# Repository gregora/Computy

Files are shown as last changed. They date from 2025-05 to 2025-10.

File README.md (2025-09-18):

# Computy

An STM32 based flight computer

## Features

- **STM32F205 MCU**
- **BNO055 IMU** and **magnetometer**
- **GNSS** via UART
- **6 PWM** outputs for servos
- Receiver connection via UART
- **433MHz CC1101** telemetry radio

## Hardware

Board specifictions:
- **50mm x 100mm** board size
- Four **M3** mounting holes
- **25Mhz** external oscilator

KiCAD files can be found in `/PCB` directory.

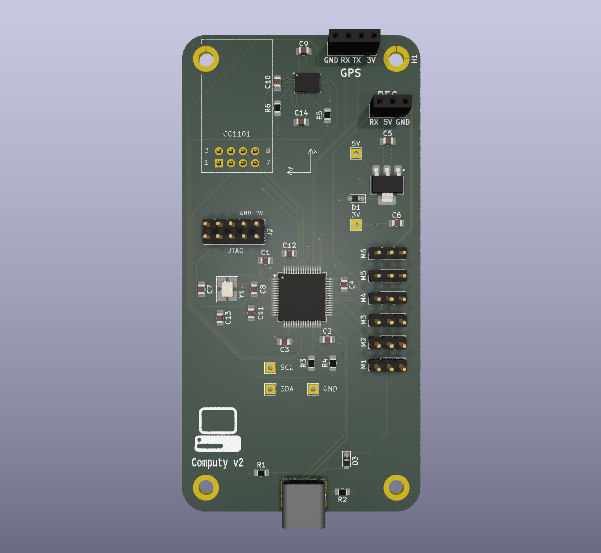
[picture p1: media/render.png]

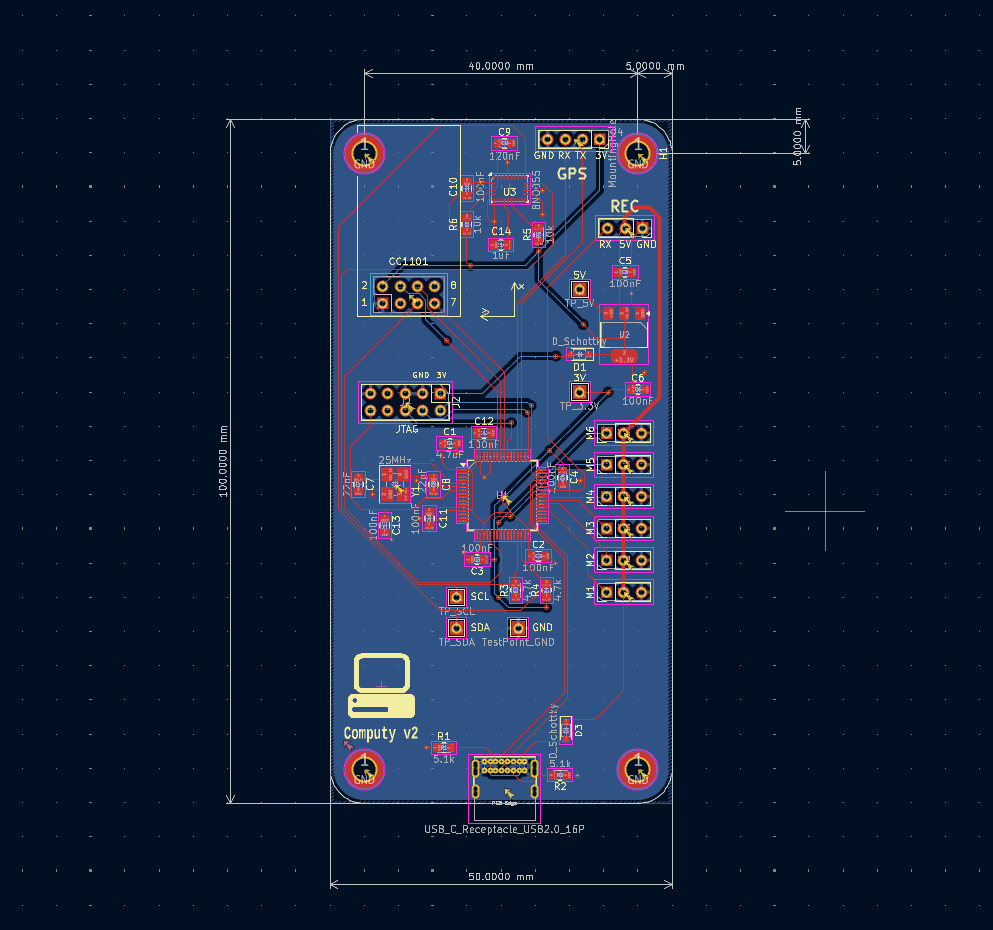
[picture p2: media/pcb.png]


## Firmware

MCU is programmed with CubeIDE. Full project is located in `firmware/Computy`.

### Dependencies

- **[stm32-nmea-gps-hal](https://github.com/sztvka/stm32-nmea-gps-hal)** (**modified** and **included**)

### Setup

Before you can build and upload the project to your Computy board, you have to create a `coordinates.h` header file in `firmware/Computy/Core/Inc` in which you have to define `TARGET_LAT` and `TARGET_LONG` variables.
Because the geolocation is sensitive, this file is included in `.gitignore` and is thus hidden.

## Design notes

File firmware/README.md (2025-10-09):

# Firmware specifications

## Operation modes

| Mode | Name | Description |
|---|---|---|
| 0 | Manual | Direct output to PWM signals |
| 1 | Take-off | Assume 10 degree pitch up attitude |
| 2 | Fly-by-wire | Control angular velocities |
| 3 | Automatic | Fly the mission autonomously |
| 255  | Recovery | Mode 0, only exit when all switches are up |

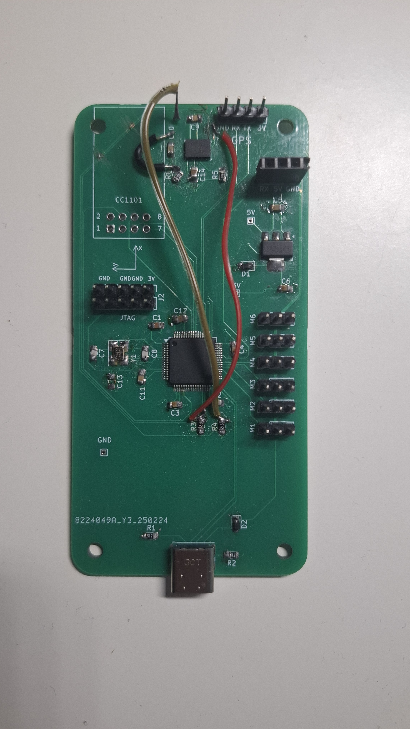
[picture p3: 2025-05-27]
media/Computy.jpg

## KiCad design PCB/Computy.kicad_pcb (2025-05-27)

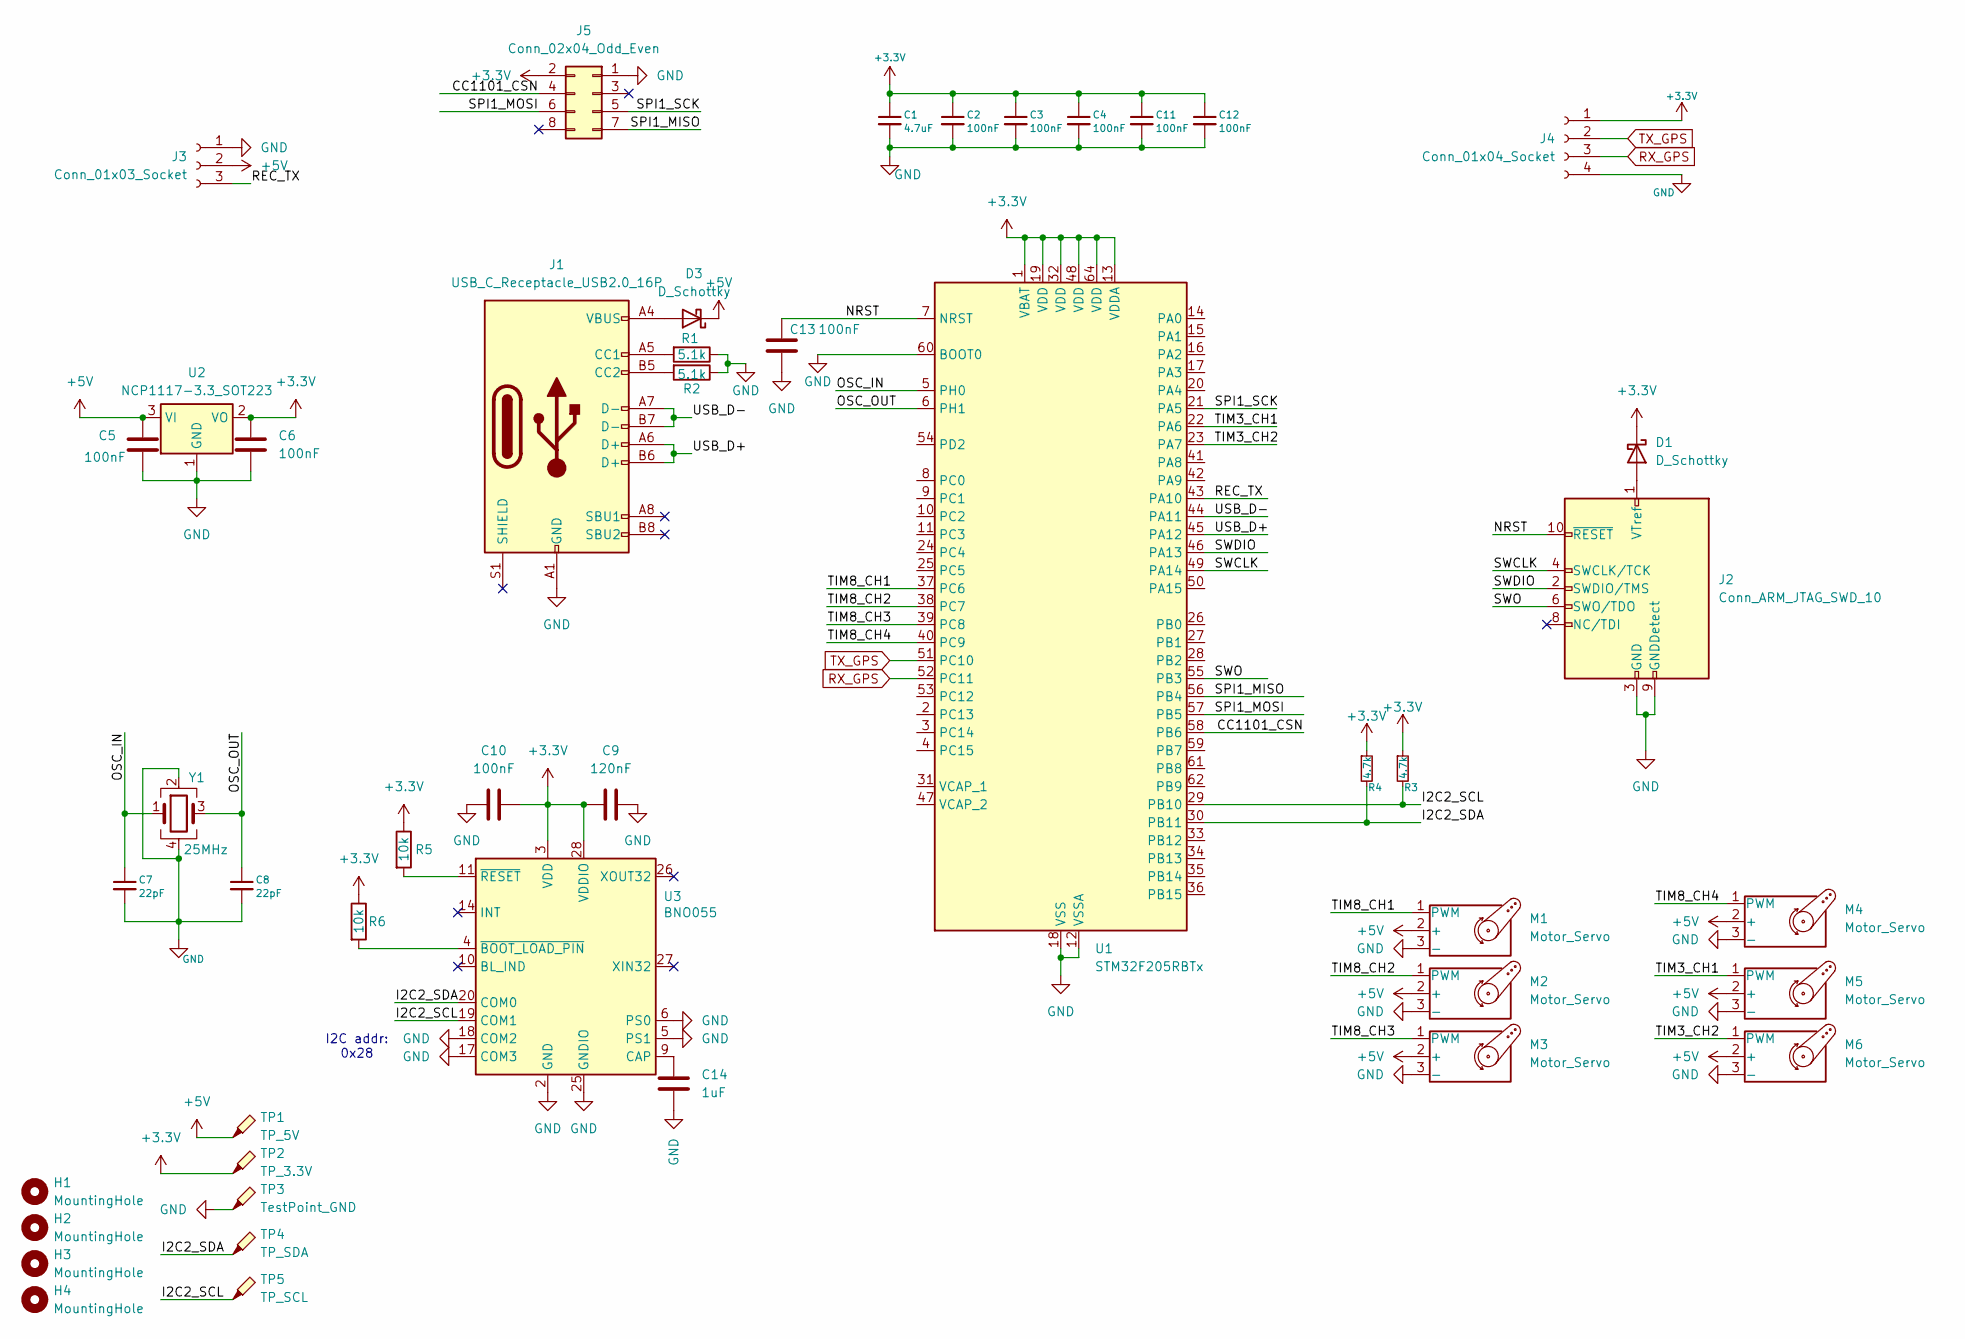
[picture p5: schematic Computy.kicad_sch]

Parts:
C1: 4.7uF; C_0805_2012Metric_Pad1.18x1.45mm_HandSolder
C2, C3, C4, C5, C6, C10, C11, C12, C13: 100nF; C_0805_2012Metric_Pad1.18x1.45mm_HandSolder
C7, C8: 22pF; C_0805_2012Metric_Pad1.18x1.45mm_HandSolder
C9: 120nF; C_0805_2012Metric_Pad1.18x1.45mm_HandSolder
C14: 1uF; C_0805_2012Metric_Pad1.18x1.45mm_HandSolder
D1, D3: D_Schottky; D_SOD-323_HandSoldering
H1, H2, H3, H4: MountingHole; MountingHole_3.2mm_M3_DIN965_Pad
J1: USB_C_Receptacle_USB2.0_16P; USB_C_Receptacle_GCT_USB4085
J2: Conn_ARM_JTAG_SWD_10; PinHeader_2x05_P2.54mm_Vertical
J3: Conn_01x03_Socket; PinSocket_1x03_P2.54mm_Vertical
J4: Conn_01x04_Socket; PinSocket_1x04_P2.54mm_Vertical
J5: Conn_02x04_Odd_Even; PinSocket_2x04_P2.54mm_Vertical
M1, M2, M3, M4, M5, M6: Motor_Servo; PinHeader_1x03_P2.54mm_Vertical
R1, R2: 5.1k; R_0805_2012Metric_Pad1.20x1.40mm_HandSolder
R3, R4: 4.7k; R_0805_2012Metric_Pad1.20x1.40mm_HandSolder
R5, R6: 10k; R_0805_2012Metric_Pad1.20x1.40mm_HandSolder
TP1: TP_5V; TestPoint_THTPad_2.0x2.0mm_Drill1.0mm
TP2: TP_3.3V; TestPoint_THTPad_2.0x2.0mm_Drill1.0mm
TP3: TestPoint_GND; TestPoint_THTPad_2.0x2.0mm_Drill1.0mm
TP4: TP_SDA; TestPoint_THTPad_2.0x2.0mm_Drill1.0mm
TP5: TP_SCL; TestPoint_THTPad_2.0x2.0mm_Drill1.0mm
U1: STM32F205RBTx; LQFP-64_10x10mm_P0.5mm
U2: NCP1117-3.3_SOT223; SOT-223-3_TabPin2
U3: BNO055; LGA-28_5.2x3.8mm_P0.5mm
Y1: 25MHz; Crystal_SMD_3225-4Pin_3.2x2.5mm_HandSoldering

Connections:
+3.3V: C1.1, C2.1, C3.1, C4.1, C6.1, C9.2, C10.2, C11.1, C12.1, D1.1 (K), J4.1, J5.2, R3.1, R4.1, R5.1, R6.1, TP2.1, U1.1 (VBAT), U1.13 (VDDA), U1.19 (VDD), U1.32 (VDD), U1.48 (VDD), U1.64 (VDD), U2.2 (VO), U3.3 (VDD), U3.28 (VDDIO)
+5V: C5.1, D3.1 (K), J3.2, M1.2 (+), M2.2 (+), M3.2 (+), M4.2 (+), M5.2 (+), M6.2 (+), TP1.1, U2.3 (VI)
/CC1101_CSN: J5.4, U1.58 (PB6)
/I2C2_SCL: R3.2, TP5.1, U1.29 (PB10), U3.19 (COM1)
/I2C2_SDA: R4.2, TP4.1, U1.30 (PB11), U3.20 (COM0)
/NRST: C13.1, J2.10 (~RESET), U1.7 (NRST)
/OSC_IN: C7.1, U1.5 (PH0), Y1.1
/OSC_OUT: C8.1, U1.6 (PH1), Y1.3
/REC_TX: J3.3, U1.43 (PA10)
/SPI1_MISO: J5.7, U1.56 (PB4)
/SPI1_MOSI: J5.6, U1.57 (PB5)
/SPI1_SCK: J5.5, U1.21 (PA5)
/SWCLK: J2.4 (SWCLK/TCK), U1.49 (PA14)
/SWDIO: J2.2 (SWDIO/TMS), U1.46 (PA13)
/SWO: J2.6 (SWO/TDO), U1.55 (PB3)
/TIM3_CH1: M5.1 (PWM), U1.22 (PA6)
/TIM3_CH2: M6.1 (PWM), U1.23 (PA7)
/TIM8_CH1: M1.1 (PWM), U1.37 (PC6)
/TIM8_CH2: M2.1 (PWM), U1.38 (PC7)
/TIM8_CH3: M3.1 (PWM), U1.39 (PC8)
/TIM8_CH4: M4.1 (PWM), U1.40 (PC9)
/USB_D+: J1.A6 (D+), J1.B6 (D+), U1.45 (PA12)
/USB_D-: J1.A7 (D-), J1.B7 (D-), U1.44 (PA11)
GND: C1.2, C2.2, C3.2, C4.2, C5.2, C6.2, C7.2, C8.2, C9.1, C10.1, C11.2, C12.2, C13.2, C14.2, H1.1, H2.1, H3.1, H4.1, J1.A1 (GND), J1.A12 (GND), J1.B1 (GND), J1.B12 (GND), J2.3 (GND), J2.5 (GND), J2.9 (GNDDetect), J3.1, J4.4, J5.1, M1.3 (-), M2.3 (-), M3.3 (-), M4.3 (-), M5.3 (-), M6.3 (-), R1.1, R2.1, TP3.1, U1.12 (VSSA), U1.18 (VSS), U1.60 (BOOT0), U1.63 (VSS), U2.1 (GND), U3.2 (GND), U3.5 (PS1), U3.6 (PS0), U3.17 (COM3), U3.18 (COM2), U3.25 (GNDIO), Y1.2, Y1.4
unnamed: D1.2 (A), J2.1 (VTref)
unnamed: D3.2 (A), J1.A4 (VBUS), J1.A9 (VBUS), J1.B4 (VBUS), J1.B9 (VBUS)
unnamed: J1.A5 (CC1), R1.2
unnamed: J1.B5 (CC2), R2.2
unnamed: C14.1, U3.9 (CAP)
unnamed: R6.2, U3.4 (~BOOT_LOAD_PIN)
unnamed: R5.2, U3.11 (~RESET)
RX_GPS: J4.3, U1.52 (PC11)
TX_GPS: J4.2, U1.51 (PC10)

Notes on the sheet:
I2C addr: 0x28

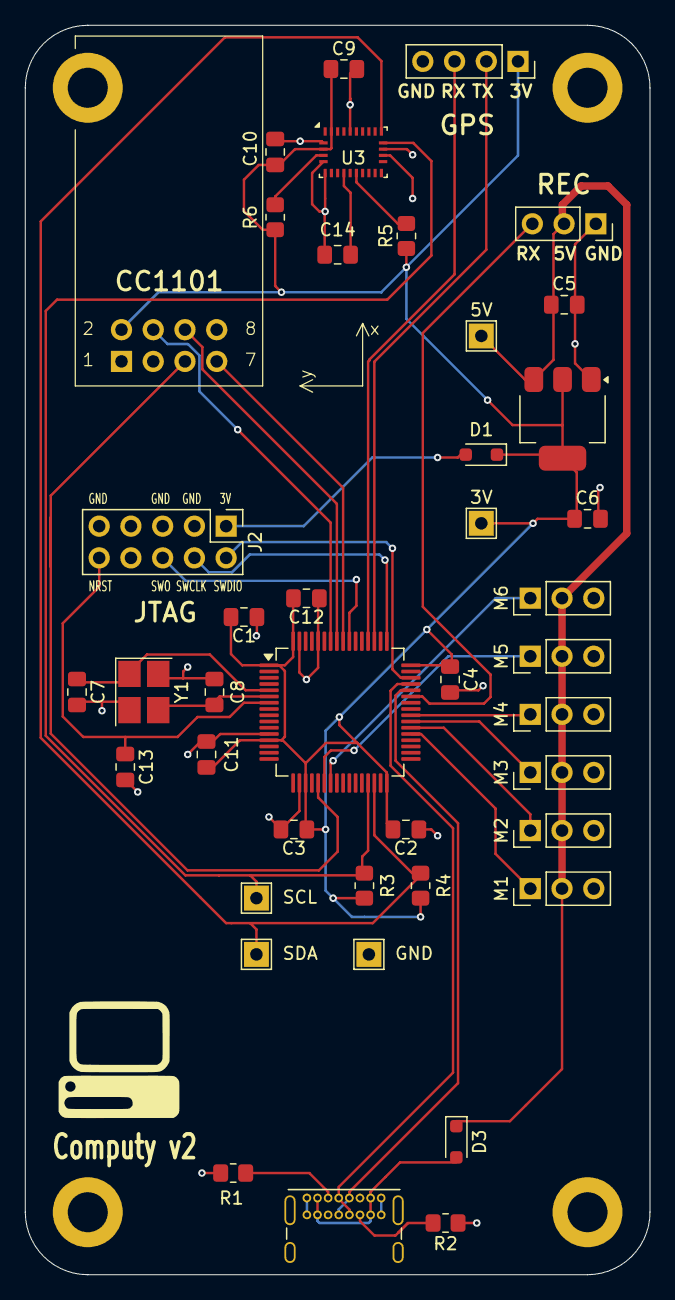
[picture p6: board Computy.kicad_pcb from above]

Board: 2 copper layers, 50.0 x 100.0 mm, 46 parts (1 on the bottom side), 33 nets.

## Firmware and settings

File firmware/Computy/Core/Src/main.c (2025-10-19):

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
/* Includes ------------------------------------------------------------------*/
#include "main.h"

/* USER CODE BEGIN Includes */
#include "nmea_parse.h"
#include "bno055.h"
#include "cc1101.h"
#include "quaternion.h"
#include "ibus.h"
#include "coordinates.h"
#define ARM_MATH_CM3
#include "arm_math.h"
#include "kalman.h"
/* USER CODE END Includes */

/* USER CODE BEGIN PD */
#define RAD2DEG  180.0f / 3.1415f

#define ELEVATOR_TRIM (int16_t)1472
#define AILERON_TRIM  (int16_t)1472
#define RUDDER_TRIM   (int16_t)1381

/* USER CODE END PD */

I2C_HandleTypeDef hi2c2;

SPI_HandleTypeDef hspi1;

TIM_HandleTypeDef htim2;
TIM_HandleTypeDef htim3;
TIM_HandleTypeDef htim8;

UART_HandleTypeDef huart4;
UART_HandleTypeDef huart1;
UART_HandleTypeDef huart6;
DMA_HandleTypeDef hdma_usart1_rx;

/* USER CODE BEGIN PV */
char rx_buff_gps[83]; // sentence buffer - NMEA messages are at most 82 chars long
char rx_char_gps;
int rx_i_gps = 0;
char nmea_sentence[83]; // actual sentence

GPS gps;
char lastMeasure[10];

uint8_t rx_buff_ibus[32]; // start - 14 channels - checksum (circular buffer)
uint16_t channels[14] = {1500, 1500, 1000, 1500, 0, 0, 0, 0, 0, 0, 0, 0, 0, 0};

struct Packet p;

int16_t target_index = 0;

float target_lat = 0;
float target_long = 0;


// Define two 2x2 matrices
float32_t dataA[4] = {1.0f, 2.0f,
                       3.0f, 4.0f};
float32_t dataB[4] = {5.0f, 6.0f,
                       7.0f, 8.0f};
float32_t dataC[4]; // output 2x2

// Matrix handles
arm_matrix_instance_f32 A, B, C;



/* USER CODE END PV */

void SystemClock_Config(void);
static void MX_GPIO_Init(void);
static void MX_DMA_Init(void);
static void MX_I2C2_Init(void);
static void MX_UART4_Init(void);
static void MX_TIM8_Init(void);
static void MX_TIM3_Init(void);
static void MX_USART1_UART_Init(void);
static void MX_SPI1_Init(void);
static void MX_TIM2_Init(void);
static void MX_USART6_UART_Init(void);
/**
  * @brief  The application entry point.
  * @retval int
  */
int main(void)
{

  /* MCU Configuration--------------------------------------------------------*/

  /* Reset of all peripherals, Initializes the Flash interface and the Systick. */
  HAL_Init();

  /* Configure the system clock */
  SystemClock_Config();

  /* Initialize all configured peripherals */
  MX_GPIO_Init();
  MX_DMA_Init();
  MX_I2C2_Init();
  MX_UART4_Init();
  MX_TIM8_Init();
  MX_TIM3_Init();
  MX_USART1_UART_Init();
  MX_SPI1_Init();
  MX_TIM2_Init();
  MX_USART6_UART_Init();
  /* USER CODE BEGIN 2 */
  HAL_TIM_PWM_Start(&htim8, TIM_CHANNEL_2);
  HAL_TIM_PWM_Start(&htim8, TIM_CHANNEL_3);
  HAL_TIM_PWM_Start(&htim8, TIM_CHANNEL_4);

  HAL_TIM_PWM_Start(&htim3, TIM_CHANNEL_1);
  HAL_TIM_PWM_Start(&htim3, TIM_CHANNEL_2);

  HAL_TIM_Base_Start(&htim2);  // Start TIM2 in polling mode

  BNO055_Handle_t bno055;
  BNO055_Quaternion_t quat;
  BNO055_LinearAccel_t accel;
  BNO055_Euler_t euler;
  BNO055_AngularVelocity_t ang_vel;

  // Initialize BNO055
  HAL_Delay(500); // NECESSARY delay
  HAL_StatusTypeDef ret;
  ret = BNO055_Init(&bno055, &hi2c2, BNO055_I2C_ADDR1);

  if(ret != HAL_OK)
  {
      // Handle error
  }

  uint32_t error;

  // Set GNSS frequency to 10Hz
  const uint8_t gnss_10hz[] = {0xB5, 0x62, 0x06, 0x08, 0x06, 0x00, 0x64, 0x00, 0x01, 0x00, 0x01, 0x00, 0x7A, 0x12};
  const uint8_t gnss_5hz[]  = {0xB5, 0x62, 0x06, 0x08, 0x06, 0x00, 0xC8, 0x00, 0x01, 0x00, 0x01, 0x00, 0xF0, 0x0D};
  const uint8_t gnss_2hz[]  = {0xB5, 0x62, 0x06, 0x08, 0x06, 0x00, 0xF4, 0x01, 0x01, 0x00, 0x01, 0x00, 0x22, 0x6A};
  const uint8_t gnss_1hz[]  = {0xB5, 0x62, 0x06, 0x08, 0x06, 0x00, 0xE8, 0x03, 0x01, 0x00, 0x01, 0x00, 0x01, 0x39};

  HAL_UART_Transmit_IT(&huart4, gnss_2hz, 14);

  /* USER CODE END 2 */

  /* Infinite loop */
  /* USER CODE BEGIN WHILE */

  HAL_UART_Receive_IT(&huart4, &rx_char_gps, 1);
  HAL_UART_Receive_DMA(&huart1, rx_buff_ibus, 32);

  uint32_t last_transmission = 0; // when was the last packet sent?

  // Axis remap necessary transformations
  struct Quaternion quat_axis_remap =     {0.0,  1.0f, 0.0, 0.0}; //  z -> -z,  y -> -y
  struct Quaternion quat_axis_remap_inv = {0.0, -1.0f, 0.0, 0.0}; // -z ->  z, -y ->  y
  struct Quaternion quat_rotate_azimuth = {0.70710678118, 0, 0, 0.70710678118}; // rotate azimuth by 90 deg
  struct Quaternion quat_raw;
  struct Quaternion temp;

  // acceleration in global coordinates
  float ax_global = 0.0f;
  float ay_global = 0.0f;
  float az_global = 0.0f;

  kalman_init();

  float bearing = 0.0f;

  uint8_t tx_buffer[2 + sizeof(p)];
  // packet header
  tx_buffer[0] = 'a';
  tx_buffer[1] = 'b';

  while (1)
  {
    /* USER CODE END WHILE */

    /* USER CODE BEGIN 3 */
	uint32_t ms = __HAL_TIM_GET_COUNTER(&htim2);
	float dt = ((float) (ms - p.time)) / 1000;
	p.time = ms;

	if(ms - last_transmission >= 30){

	    memcpy(tx_buffer + 2, &p, sizeof(p));
	    HAL_UART_Transmit(&huart6, tx_buffer, sizeof(tx_buffer), 100);
	    last_transmission = ms;
	}

	if(BNO055_ReadQuaternion(&bno055, &quat) == HAL_OK)
	{
	    // Use quaternion data (quat.w, quat.x, quat.y, quat.z)
		quat_raw.w = quat.w;
		quat_raw.x = quat.x;
		quat_raw.y = quat.y;
		quat_raw.z = quat.z;

		// Transform vector into original space (a_inv), apply q, transform back into re-mapped space (a)
		// a * q * a_inv
		temp = quaternion_multiply(&quat_axis_remap, &quat_raw);
		temp = quaternion_multiply(&temp, &quat_axis_remap_inv);

		// Rotate azimuth by 90 degrees, to align vector to NED
		temp = quaternion_multiply(&quat_rotate_azimuth, &temp);

		// Set quaternion
		p.quat = temp;

		BNO055_QuaternionToEuler(&p.quat, &euler);

	}



    // Read linear acceleration
    if(BNO055_ReadLinearAccel(&bno055, &accel) == HAL_OK)
    {
        // Use acceleration data (accel.x, accel.y, accel.z in m/s^2)
    	float raw_accel[3] = {accel.x, accel.y, accel.z};

    	// Calculate acceleration in global coordinates
		temp = quaternion_multiply(&quat_axis_remap, &quat_raw);
		temp = quaternion_multiply(&quat_rotate_azimuth, &temp);


    	struct Quaternion a_global = quaternion_transform_vector(&temp, raw_accel);

    	ax_global = a_global.x;
    	ay_global = a_global.y;
    	az_global = a_global.z;

    	// acceleration is no longer in packet!
    	//p.ax = ax_global;
    	//p.ay = ay_global;
    	//p.az = az_global;

    	//kalman_predict(dt, ax_global, ay_global, az_global);
    	//float kalman_latitude, kalman_longitude, kalman_height;
    	//kalman_result(&kalman_latitude, &kalman_longitude, &kalman_height);

    	//p.latitude = kalman_latitude;
    	//p.longitude = kalman_longitude;
    	//p.altitude = kalman_height;

    }


    if(BNO055_ReadAngularVelocity(&bno055, &ang_vel) == HAL_OK) {
    	p.p = ang_vel.x;
    	p.q = ang_vel.y;
    	p.r = ang_vel.z;
    }

    // Parse GPS
	nmea_parse(&gps, nmea_sentence);

	// Check if new measurement has been read
    if (gps.fix == 1 && strcmp(gps.lastMeasure, lastMeasure) != 0){
		strcpy(lastMeasure, gps.lastMeasure);


		p.latitude = gps.latitude;
		p.longitude = gps.longitude;
		p.altitude = gps.altitude;
		p.satellites = gps.satelliteCount;


		//kalman_update(gps.latitude, gps.longitude, gps.altitude);

		target_lat = latitudes[target_index];
		target_long = longitudes[target_index];

		// Calculate distance from target position
		float delta_x = (target_lat  - p.latitude)  / 360.0f * EARTH_CIRCUMFERENCE;
		float delta_y = (target_long - p.longitude) / 360.0f * EARTH_CIRCUMFERENCE * cos(target_lat / 180.0f * 3.1415);

		float distance_to_target = sqrt(delta_x*delta_x + delta_y*delta_y);

		// Objective complete if the aircraft is within 20m
		if (distance_to_target < 30.0f){
			target_index = (target_index + 1) % num_points;
		}

		// Calculate bearing from target position and current position
		bearing = RAD2DEG * atan2(
				sin((target_long - p.longitude) / RAD2DEG) * cos(target_lat / RAD2DEG),
				cos(p.latitude / RAD2DEG) * sin(target_lat / RAD2DEG) - sin(p.latitude / RAD2DEG) * cos(target_lat / RAD2DEG) * cos((target_long - p.longitude)/RAD2DEG)
		);
    }

    // Parse iBus
	parse_ibus(rx_buff_ibus, channels);

	// Choose control law
	// Mode 0 - Manual
	if      (channels[4] == 1000 && channels[5] == 1000 && channels[6] == 1000){
		p.mode = 0;
	}
	// Mode 1 - Take-off
	else if (channels[4] == 2000 && channels[5] == 1000 && channels[6] == 1000 && (p.mode == 0 || p.mode == 1)){
		p.mode = 1;

		// Also enter recovery mode if attitude control sticks are not centered
		if (abs(channels[0] - AILERON_TRIM) > 100){
			p.mode = 255;
		}
		if (abs(channels[1] - ELEVATOR_TRIM) > 100){
			p.mode = 255;
		}
		if 	(abs(channels[3] - RUDDER_TRIM) > 100){
			p.mode = 255;
		}
	}

	// Mode 3 - Automatic
	else if (channels[4] == 1000 && channels[5] == 1000 && channels[6] == 1500 && (p.mode == 0 || p.mode == 3)){
		p.mode = 3;

		// Also enter recovery mode if attitude control sticks are not centered
		if (abs(channels[0] - AILERON_TRIM) > 100){
			p.mode = 255;
		}
		if (abs(channels[1] - ELEVATOR_TRIM) > 100){
			p.mode = 255;
		}
		if (abs(channels[3] - RUDDER_TRIM) > 100){
			p.mode = 255;
		}
	}

	// Mode 255 - Recovery
	else {
		p.mode = 255;
	}


	// Respond to mode
	if (p.mode == 0 || p.mode == 255){
		// Map channels directly
	    for (int i = 0; i < 7; i++){
	    	p.channels[i] = channels[i];
	    }
	} else if (p.mode == 1){
		p.channels[0] = AILERON_TRIM  + (int16_t) (500.0f*((euler.roll*RAD2DEG  -  0.0f)*0.0110f + (ang_vel.x)*0.0022f));
		p.channels[1] = ELEVATOR_TRIM + (int16_t) (500.0f*((euler.pitch*RAD2DEG - 10.0f)*0.0200f - (ang_vel.y)*0.0040f));
		p.channels[3] = RUDDER_TRIM;

		// Map channels 4-7 directly
		for(int i = 4; i < 7; i++){
			p.channels[i] = channels[i];
		}
	} else if (p.mode == 3){
		// P controller for bearing
		float roll_target = 1.00f * (fmod(bearing - euler.yaw*RAD2DEG + 180, 360) - 180.0f);

		// Do not exceed 50 deg of roll
		if (roll_target > 50) {
			roll_target =  50;
		}else if (roll_target < -50){
			roll_target = -50;
		}

		float pitch_factor = cos(euler.roll);
		if (pitch_factor < 0.3){
			pitch_factor = 0.3;
		}

		float pitch_target = 4.0f + 50.0f * (1 - pitch_factor);

		p.channels[0] = AILERON_TRIM  + (int16_t) (500.0f*((euler.roll*RAD2DEG  -  roll_target)*0.0110f + (ang_vel.x)*0.0022f));
		p.channels[1] = ELEVATOR_TRIM + (int16_t) (500.0f*((euler.pitch*RAD2DEG - pitch_target)*0.0200f - (ang_vel.y)*0.0040f));
		p.channels[3] = RUDDER_TRIM;

		// Map channels 4-7 directly
		for(int i = 4; i < 7; i++){
			p.channels[i] = channels[i];
		}
	}

	// Limit channel values
	for (int i = 0; i < 7; i++){
		if (p.channels[i] < 1000){
			p.channels[i] = 1000;
		}
		if (p.channels[i] > 2000){
			p.channels[i] = 2000;
		}
	}

    // Apply actuation values
    TIM8->CCR2 = p.channels[0] - 500;
    TIM8->CCR3 = p.channels[1] - 500;
    TIM8->CCR4 = p.channels[2] - 500;

    TIM3->CCR1 = p.channels[3] - 500;
    TIM3->CCR2 = p.channels[4] - 500;



  }
  /* USER CODE END 3 */
}

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
/* USER CODE BEGIN 4 */


void HAL_UART_RxCpltCallback(UART_HandleTypeDef *huart)
{

	if(huart->Instance == USART1){
		// Do nothig - we are using circular buffer
	}else if(huart->Instance == UART4){

		HAL_UART_Receive_IT(&huart4, &rx_char_gps, 1);

		// Handle GPS RX
		if(rx_char_gps == '$'){
			rx_buff_gps[rx_i_gps + 1] = '\r';
			rx_buff_gps[rx_i_gps + 2] = '\n';
			rx_buff_gps[rx_i_gps + 3] = '\0';

			rx_i_gps = 0;

			memcpy(nmea_sentence, rx_buff_gps, 83);

			for (int i = 0; i < 83; i++){
				rx_buff_gps[i] = '\0';
			}

		}

		if(rx_i_gps >= 83){
			rx_i_gps = 0;
		}

		rx_buff_gps[rx_i_gps] = rx_char_gps;
		rx_i_gps += 1;
	}
}

int __io_putchar(int ch)
{
 // Write character to ITM ch.0
 ITM_SendChar(ch);
 return(ch);
}

/* USER CODE END 4 */
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


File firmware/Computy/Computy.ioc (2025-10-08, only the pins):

Mcu.UserName=STM32F205RBTx
PA10.Signal=USART1_RX
PA13.Signal=SYS_JTMS-SWDIO
PA14.Signal=SYS_JTCK-SWCLK
PA5.Signal=SPI1_SCK
PA6.Signal=S_TIM3_CH1
PA7.Signal=S_TIM3_CH2
PA9.Signal=USART1_TX
PB10.Signal=I2C2_SCL
PB11.Signal=I2C2_SDA
PB3.Signal=SYS_JTDO-SWO
PB4.Signal=SPI1_MISO
PB5.Signal=SPI1_MOSI
PB6.Signal=GPIO_Output
PC10.Signal=UART4_TX
PC11.Signal=UART4_RX
PC6.Signal=USART6_TX
PC7.Signal=S_TIM8_CH2
PC8.Signal=S_TIM8_CH3
PC9.Signal=S_TIM8_CH4
PH0-OSC_IN.Signal=RCC_OSC_IN
PH1-OSC_OUT.Signal=RCC_OSC_OUT

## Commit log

2025-05-21 Add firmware
    [Computy Debug.cfg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]
2025-05-21 Update .gitignore and minor changes to the PCB
    [Computy.kicad_pcb]
2025-05-27 Computy v2
    - Fix issues with the PCB
    - Connect SWO
    - Connect CC1101 to SPI1
    - Fix BNO055 SCL and SDA
    - Add more testpoints
    - Update firmware
    - Add most recent datasheets
    [Computy.kicad_pcb, Computy.kicad_sch]
2025-05-27 Update media
    [Computy.kicad_pcb]
2025-05-27 Minor changes to PCB
    [Computy.kicad_pcb]
2025-05-27 Minor PCB changes
    [Computy.kicad_pcb]
2025-05-29 Measure fixes per second for the GPS
    [main.c]
2025-06-15 Add the library for reading data from IMU
2025-06-15 Read angular velocity
2025-06-15 Major fix - Set I2C2 to high speed mode which seems to fix HAL_BUSY error
    [Computy.ioc, main.c]
2025-06-15 Change duty cycle for i2c2
2025-06-19 Add CC1101 drivers
2025-07-30 Update IMU reading with 'software' axis remapping
2025-07-30 MAJOR: Final fix for axis remapping
    [main.c]
2025-07-31 iBus to PWM bug fix
    [main.c]
2025-07-31 Fix I2C on startup bug - Add delay of 500ms
    [Computy.ioc, main.c]
2025-08-17 Correctly implement checksum for ibus
    [main.c]
2025-08-17 Only accept ibus messages with the correct checksum
    [main.c]
2025-08-17 Add D component to PID for Mode 1
2025-08-22 Add DMA ibus reading
2025-08-24 Remove unnecessary DMA calls
2025-09-13 Fix transformation to NED (north-east-down)
    [main.c]
2025-09-13 Add P controller for bearing
2025-09-13 Update P values for bearing
2025-09-15 Update PID values
2025-09-18 Correctly add CMSIS-DSP library
    [main.c]
2025-09-20 First working version with Kalman filter
2025-09-20 Correct acceleration local to global transformation
    [main.c]
2025-10-01 [UNTESTED] Increase pitch gains and add bank angle compensation
2025-10-08 Add ground station software for 3dr radio
2025-10-09 Add rotating bug when drawing position
    [ground.py]
2025-10-09 Move ground serial data reading to a separate thread
2025-10-10 Ground control bug fixes
    [ground.py, main.c]
2025-10-10 Update timeouts and ground station
2025-10-11 Bug fixes on ground station
    [ground.py]
2025-10-17 Ground station bug fixes
    [ground.py, main.c]
2025-10-18 Add connect and disconnect sound effects to ground station
2025-10-19 Set GPS frequency to 2Hz
2025-10-19 Add angular velocities to the packet instead of accelerations

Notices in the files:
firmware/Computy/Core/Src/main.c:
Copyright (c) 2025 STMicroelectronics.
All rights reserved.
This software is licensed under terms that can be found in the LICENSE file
